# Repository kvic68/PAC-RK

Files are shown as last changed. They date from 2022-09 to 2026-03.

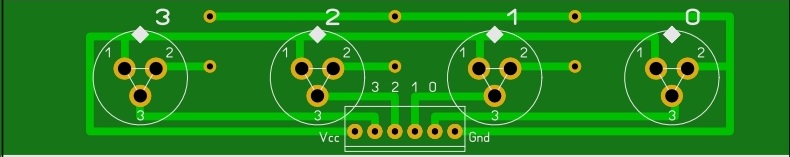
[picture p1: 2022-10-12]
INFO/GX12.JPG

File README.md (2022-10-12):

Предлагаемое устройство представляет собой программно-аппаратный комплекс контроля и управления ректификационной колонной.
Состав комплекса:
- регулятор напряжения со стабилизацией;
- контроллер насоса на шаговом двигателе;
- четырехканальный измеритель температуры с управляющей логикой;
- устройства индикации и управления;
- радио модуль  для удаленного управления по Bluetooth;
- измеритель атмосферного давления на BMP180. Реализует функцию показометра, ничем не   управляет. Можно смотреть динамику атмосферного давления во внешней программе;
- программное обеспечение для удаленного управления, логирования, медитации на разноцветные графики (под Windows).

Обсуждение тут: https://alcodistillers.ru/forum/viewtopic.php?id=2110

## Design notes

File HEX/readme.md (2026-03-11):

1.	regulator.hex – прошивка стабилизатора, заливать в Atmega328;
2.	control.hex – прошивка контроллера температуры, насоса и прочего, только в Atmega328.

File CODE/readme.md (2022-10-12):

Набор исходных текстов на ассемблере. Выполнено в Avr Studio 4.19 
1.	REGULATOR – исходники стабилизатора;
2.	CONTROL – исходники контроллера температуры, насоса и прочего.

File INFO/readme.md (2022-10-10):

1.	specification.pdf (docx) – описание работы комплекса;
2.	bill-of-materials.pdf (xls) – практически полный список деталей;
3.	scheme.spl7 – схема в формате Splan7.0, sheme.gif – она же картинкой;
4.	plate.lay6 – вариант печатной платы в формате Sprint Layout 6, plate-top.gif и plate-bottom.gif – она же в виде картинок, вид сверху и снизу.

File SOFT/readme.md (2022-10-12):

Программа управления комплексом.
Скопировать оба файла в отдельную папку и запустить исполняемый.

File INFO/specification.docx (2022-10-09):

Предлагаемое устройство представляет собой программно-аппаратный комплекс контроля и управления ректификационной колонной.

Состав комплекса:

- регулятор напряжения со стабилизацией;

- контроллер насоса на шаговом двигателе;

- четырехканальный измеритель температуры с управляющей логикой;

- устройства индикации и управления;

- радио модуль для удаленного управления по Bluetooth;

- измеритель атмосферного давления на BMP180. Реализует функцию показометра, ничем не управляет. Можно смотреть динамику атмосферного давления во внешней программе;

- программное обеспечение для удаленного управления, логирования, медитации на разноцветные графики (под Windows).

Регулятор напряжения

Обеспечивает стабильное напряжение на нагрузке не выше входного.

Работает в трех режимах:

- стабилизация,

- разгон,

- выключено.

Имеет возможность подключения дополнительного устройства нагрева при разгоне.

Есть вход аварийного отключения от внешнего датчика.

Аварийное выключение от внешнего источника одновременно останавливает отбор, включает звуковую и световую сигнализацию и блокирует всё удалённое управление.

Контроллер насоса

Управляет насосом на шаговом двигателе, обеспечивает

- равномерную скорость отбора в диапазоне 10-3000 мл/час,

- измерение общего объема отбора,

- режим дозирования (автостоп при достижении заданного объема отбора 10-5000 мл).

Измеритель температуры.

Использует датчики на базе DS18B20.

Четыре независимых канала реализуют следующие функции:

1. Измерение температуры.
2. Контроль достижения и превышения порога.
3. Исполнение установленных действий при достижении(превышении) порога.
4. Один из каналов (любой) дополнительно может осуществлять функцию «контроль разгона», т.е. при достижении температурой установленной величины, переключать режим работы стабилизатора из «разгон» в «поддержание установленного напряжения». Режим «разгон» включается в модуле стабилизатора, требуемое напряжение там же.

Измерение температуры производится одновременно по четырем независимым каналам. Измеренное значение выводится на дисплей. Если датчик неисправен или отсутствует, выводятся черточки.

Контроль превышения порога может быть либо включен, либо выключен.

Если контроль включен, то при превышении порога в любом случае подается сигнал на один из выходов контроллера. Сигнал имеет уровень логического нуля и может быть использован для управления внешними устройствами.

Кроме этого можно включить дополнительные «реакции»:

- включить звуковой сигнал,

- остановить отбор,

- выключить нагрев.

«Реакции» можно комбинировать.

Реакция «выключить нагрев» приравнена к аварийному сигналу выключения регулятора.

Управление

Осуществляется двумя энкодерами типа EC-11 со встроенной кнопкой. Один управляет регулятором напряжения, второй – контроллером насоса и, через систему меню, настройками измерителя температуры, режимами отбора, калибровкой насоса, контролем режима разгона.

Индикация

Всё выводится на OLED дисплей размером 2.42’ или более, разрешением 128х64.

Регулятор напряжения имеет свой OLED дисплей размером 0.96 дюйма. Не обязателен.

Оба дисплея должны иметь подключение по шине i2c.

Основной экран

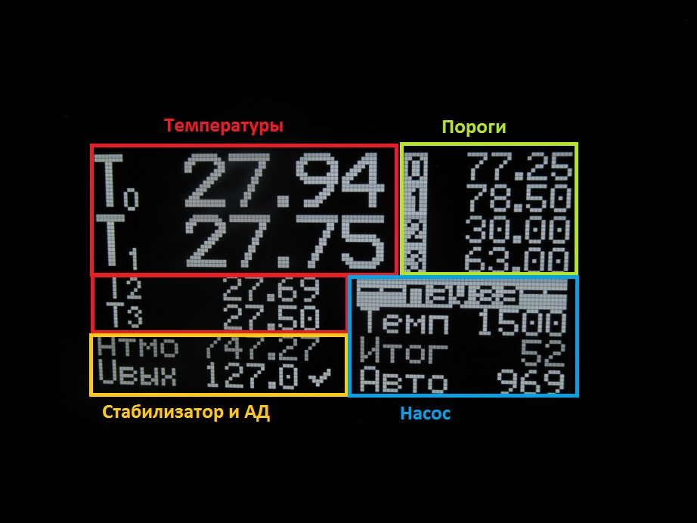
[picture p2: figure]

Блок температур просто отображает значения температуры, измеренные соответствующими датчиками. Если датчик отсутствует или выдаёт некорректные значения, то на дисплей выводится --.--

Блок порогов показывает установленные пороги срабатывания для каждого из датчиков независимо от наличия датчика. Номер датчика отображается в инверсном виде, если установлена какая-нибудь реакция на превышение порога, иначе отображение номера датчика неинверсное. При срабатывании датчика значение порога выводится в инвертированном виде.

Атмосферное давление просто выводится как информация к размышлению.

Насосная часть показывает текущее состояние насоса, скорость отбора мл/час, общий счетчик отбора в мл, остаток до автостопа в мл.

Энкодер №1, управление стабилизатором напряжения.

Логика работы.

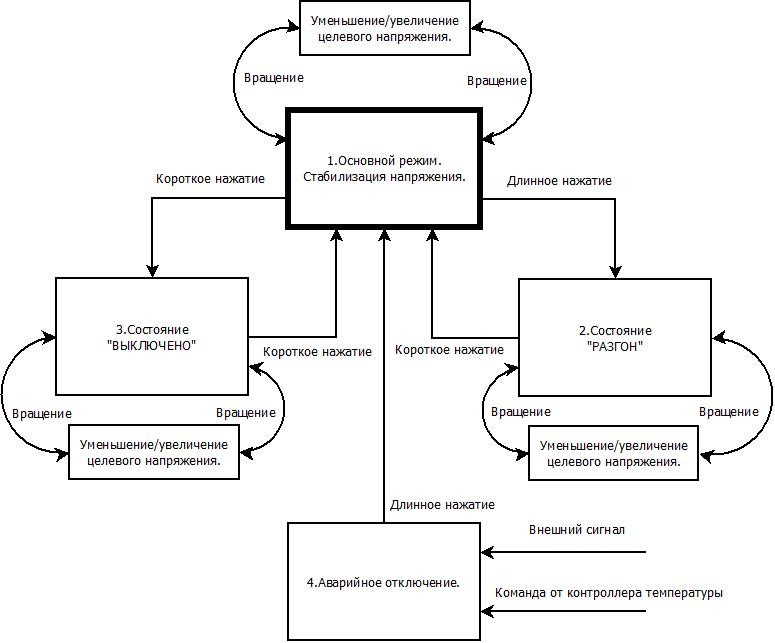
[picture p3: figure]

Отображение режимов работы стабилизатора(примеры).

1.Режим стабилизации.

Справа от значения выходного напряжения значок стабилизации. Показывает, что напряжение находится в коридоре +-0.3 вольта от заданного.

Установка желаемого напряжения призводится вращением ручки энкодера.

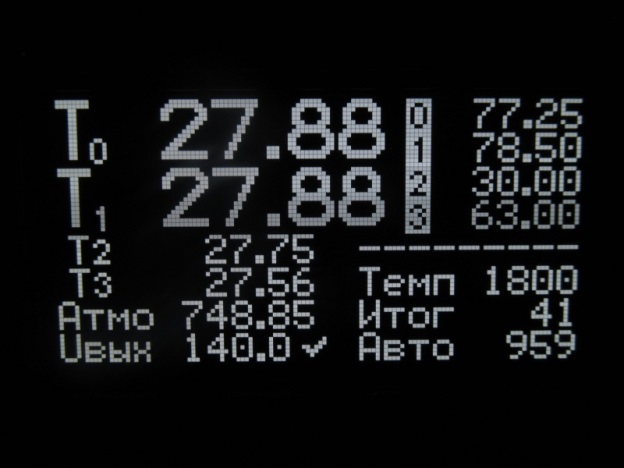
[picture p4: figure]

2.Режим разгона, включен контроль по датчику Т1 при достижении 60 градусов разгон будет выключен и осуществлён переход к напряжению стабилизации 140.0 вольт(в данном случае).

Установка напряжения стабилизации – вращением энкодера.

Вход в режим – длинное нажатие, выход – короткое нажатие.

2.Режим разгона без контроля температуры.

Всё то же самое, только разгон будет продолжаться до бесконечности, если только не отработает реакцию выключения нагрева один из датчиков. Но это уже будет аварийное отключение.

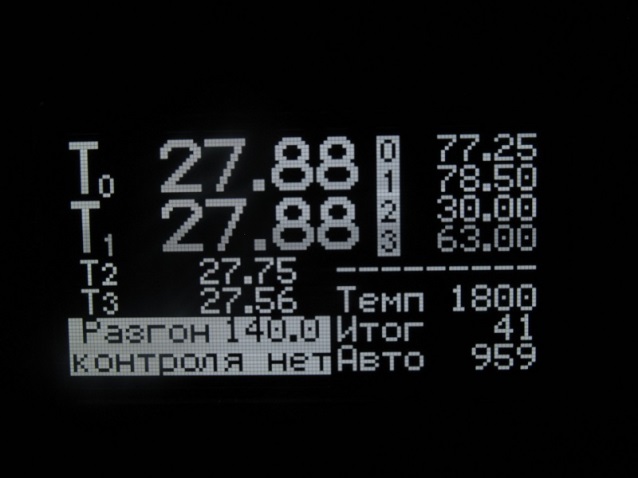
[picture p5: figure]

3.Принудительное отключение нагрева.

Вход в режим и выход из него – короткое нажатие.

4.Отключение аварийным сигналом.

Аварийный сигнал может быть подан на вход устройства либо сгенерирован блоком измерения и контроля температур.

Выход из режима – длинное нажатие на энкодер регулятора напряжения. Если аварийный сигнал не снят, произойдет возврат в режим аварийного отключения.

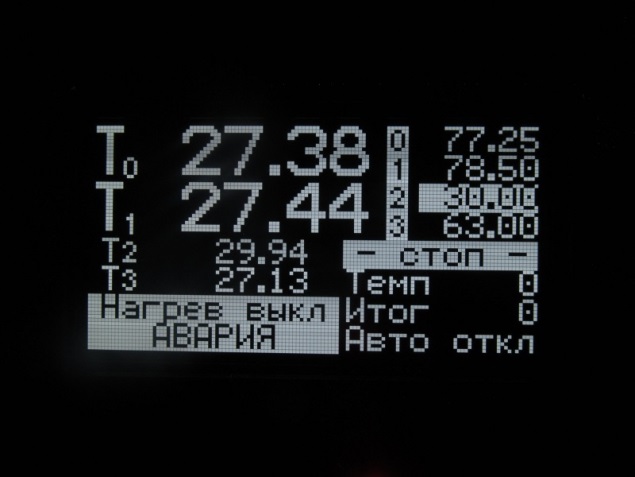
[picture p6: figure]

Энкодер №2, управление насосом и настройками аппарата.

Логика работы.

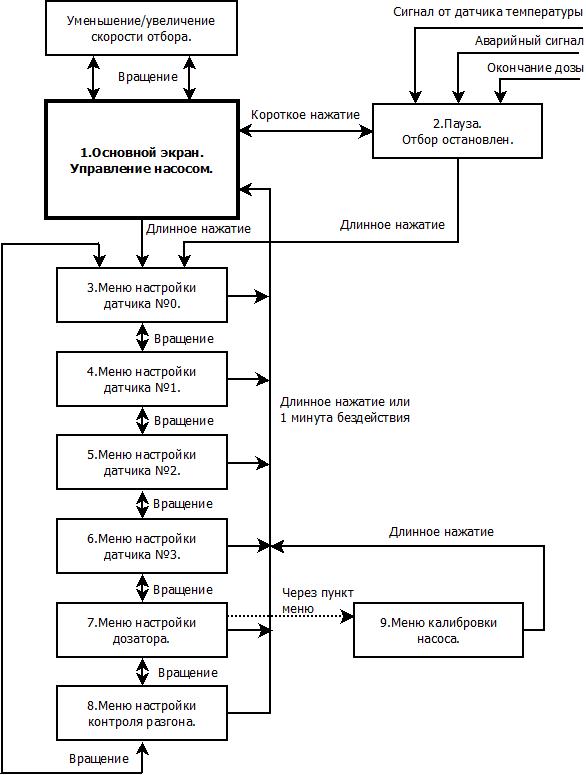
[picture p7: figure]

1.Основной экран.

Вращение энкодера №2 в основном экране приводит к изменению скорости отбора.

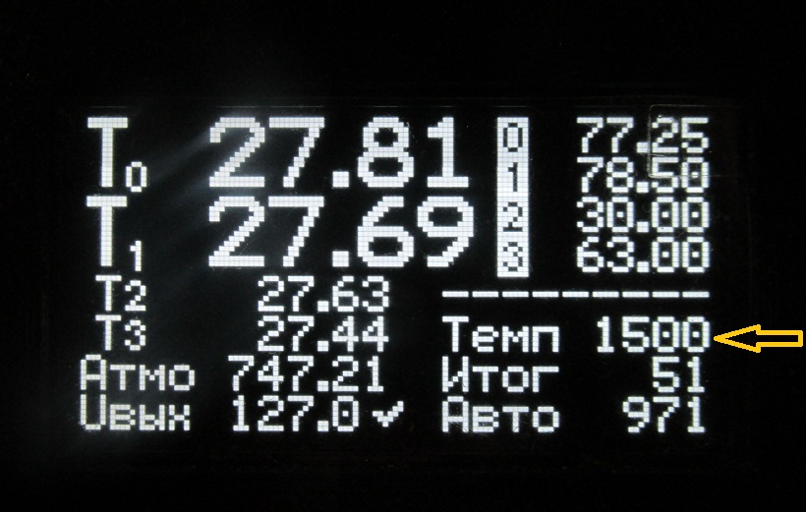
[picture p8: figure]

2. Короткое нажатие (клик) – пауза или продолжение отбора.

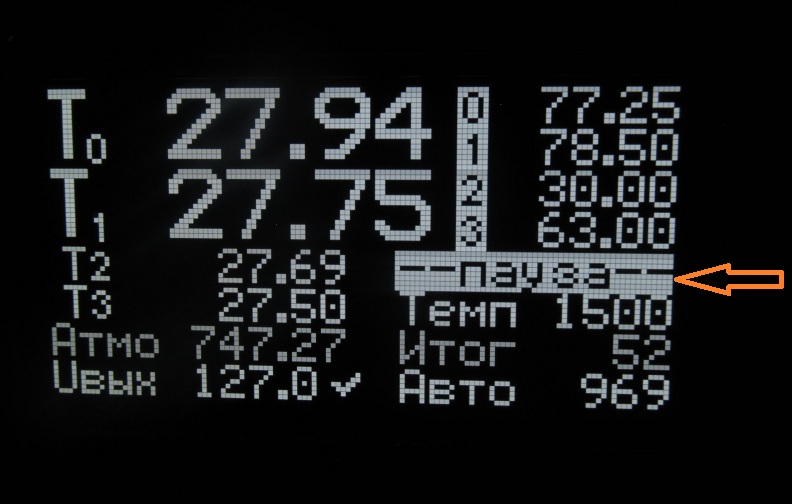
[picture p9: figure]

Длинное нажатие как в режиме рабочего хода, так и в паузе, вызывает переход к выбору экранов настройки температурных датчиков, настройки шага автостопа(дозатор), контроля разгона, калибровки насоса. Выбор датчика или другой настройки осуществляется вращением энкодера. Переход к настройке – короткое нажатие(клик).

3.4.5.6. Меню настройки температурного датчика 0.1.2.3.

Логика настройки температурного датчика.

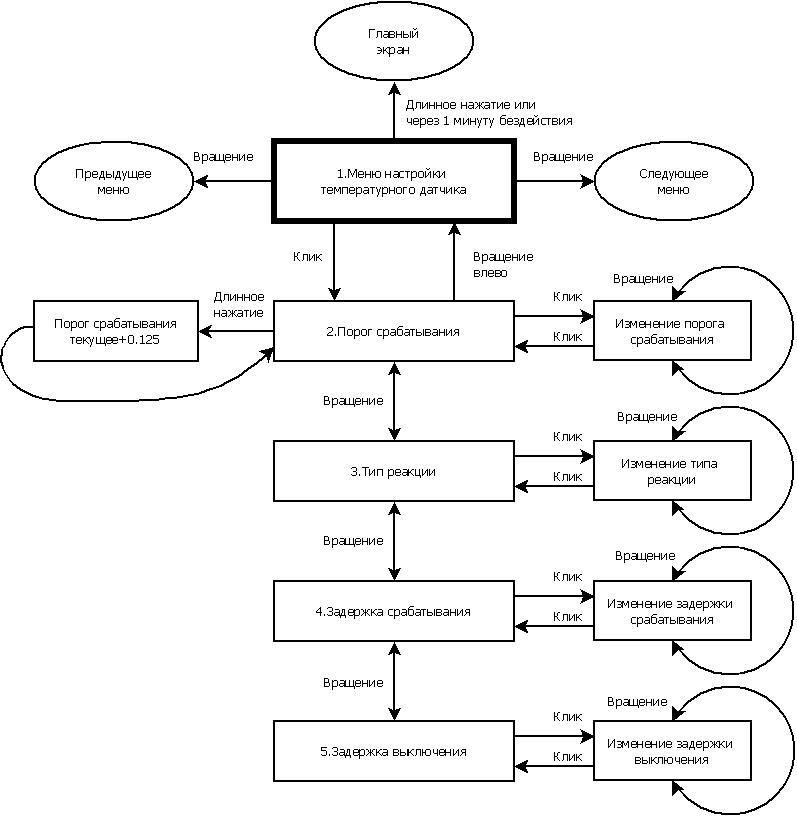
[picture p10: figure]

Порог срабатывания – величина температуры, при которой будут произведены действия, настроенные в пункте «Тип реакции».

Типы реакции:

1. Включить сигнализацию. *
2. Включить звуковой сигнал. ♩
3. Остановить отбор. ││
4. Выключить нагрев. ↓

Последовательность переключения реакций:

- выключено всё;

- включено(выдаёт сигнал на выход и зажигает

индикатор, если он установлен); *

- включено+звук; * ♩

- включено+стоп; * ││

- включено+звук+стоп; * ♩ ││

- включено+нагрев выкл.; * ↓

- включено+звук+нагрев выкл.; * ♩ ↓

- включено+стоп+нагрев выкл.; * ││ ↓

- включено+звук+стоп+нагрев выкл.; * ♩ ││ ↓

«Выключить нагрев» блокирующий. Т.е. при срабатывании этого действия, после остывания датчика автоматический возврат к нагреву не произойдёт. Необходимо участие оператора непосредственно у аппарата. Удалённо включить тоже не получится. Кроме этого при выключении нагрева будет остановлен и блокирован отбор.

Задержка срабатывания – время, которое должно пройти после достижения(превышения) порога до момента срабатывания установленных реакций.

Задержка выключения – то же самое, только при переходе через порог вниз.

Экран настройки датчика (пример):

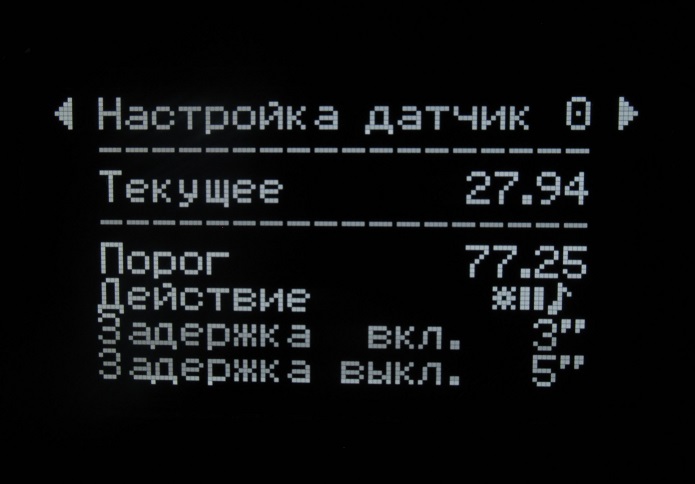
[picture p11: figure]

Температура на датчике 0 равна 27.94 градуса. При достижении значения 77.25 градуса и удержании на этом уровне или выше в течение 3 секунд будет подан сигнал на выход 0, остановлен отбор и включён звуковой сигнал. При снижении температуры ниже порога через 5 секунд будет произведен возврат к нормальному режиму работы.

7. Настройка дозатора.

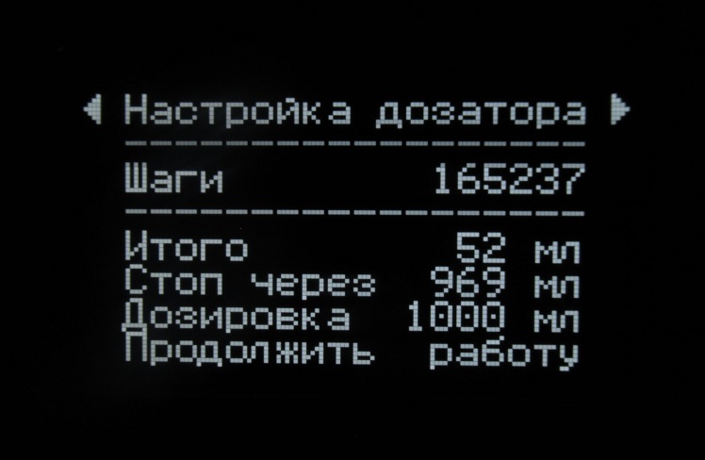
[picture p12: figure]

Доступны три пункта для изменения: «Итого», «Дозировка», «Продолжить…»

Через «Итого» можно сбросить общий счетчик отбора.

«Дозировка» - объем, после которого отбор будет остановлен.

Последний пункт комбинированный, состоит из четырех подпунктов:

- «продолжить работу» – переход в основной экран;

- «продолжить в паузе» – то же самое, только отбор будет на паузе;

- «назад к настройкам» – возврат к настройке дозатора;

- «калибровка насоса» – переход в меню калибровки насоса.

Логика настройки дозатора.

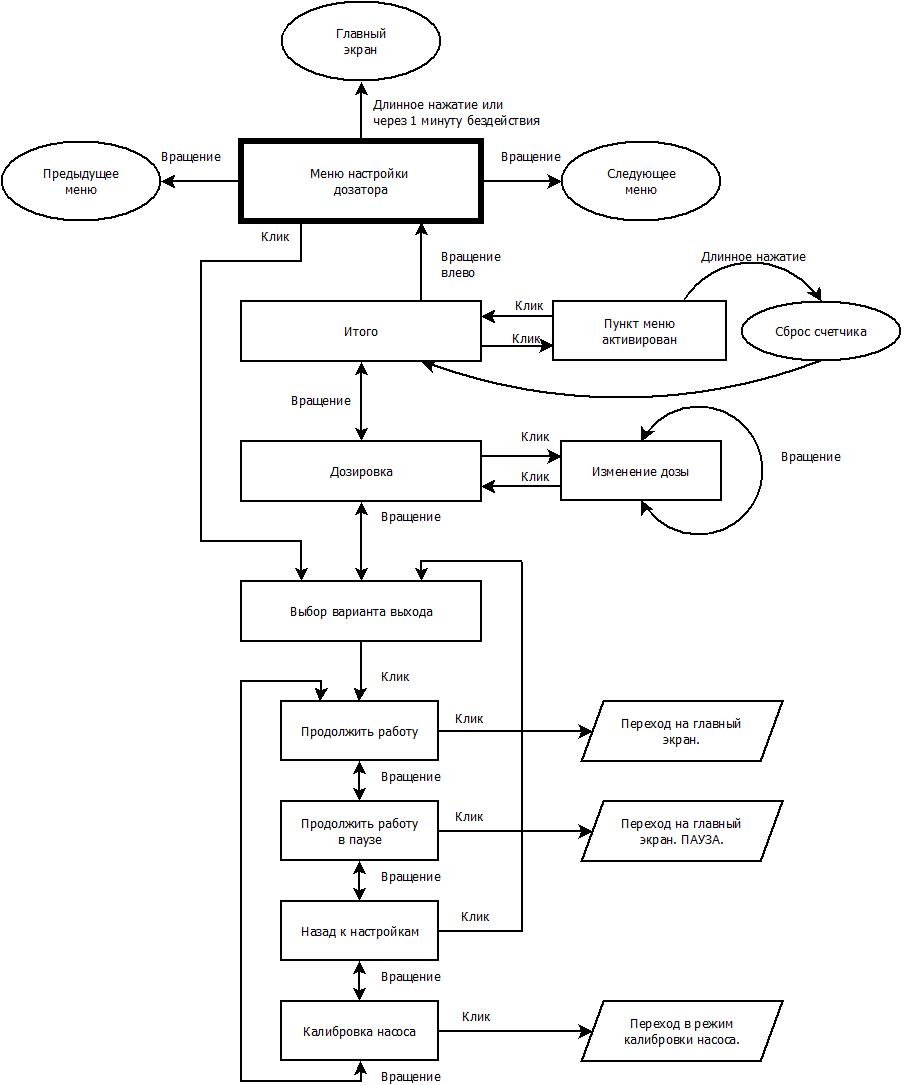
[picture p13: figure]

Режим калибровки насоса.

Доступны строки «Счетчик» и «Записать в «EEPROM».

Логика в режиме калибровки.

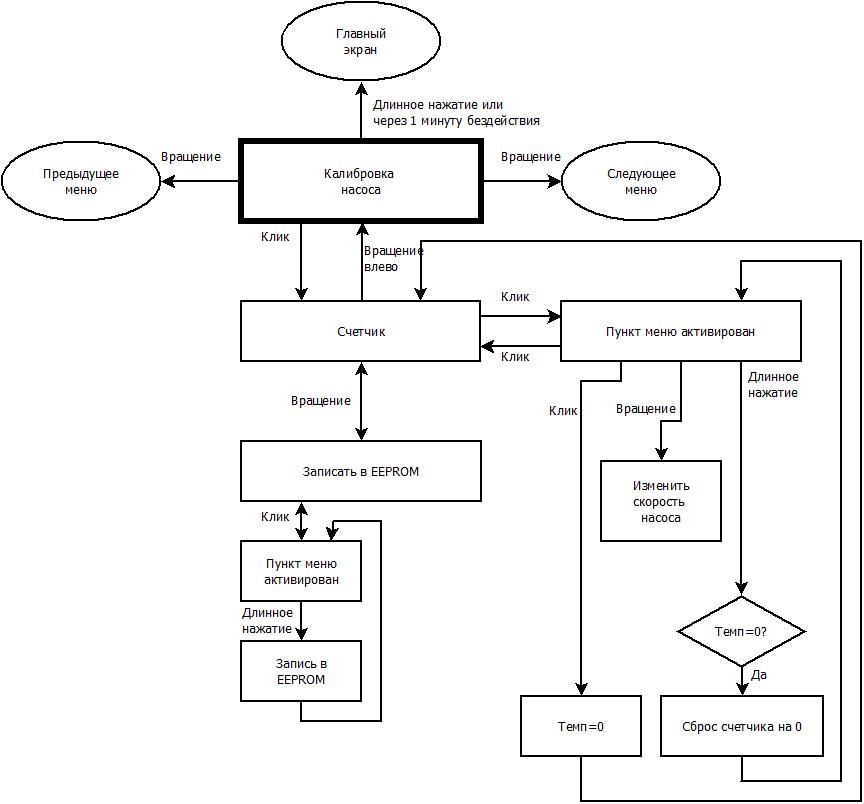
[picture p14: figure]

8. Контроль разгона.

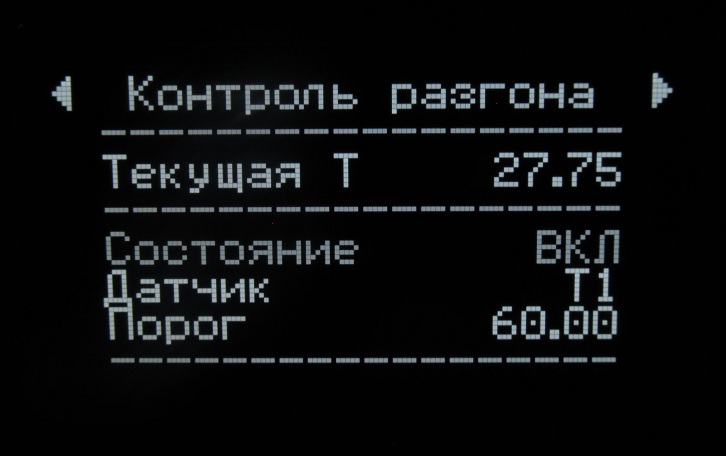
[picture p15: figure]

Можно включить или выключить («Состояние»).

Изменить датчик, осуществляющий контроль («Датчик»).

Изменить порог срабатывания («Порог»).

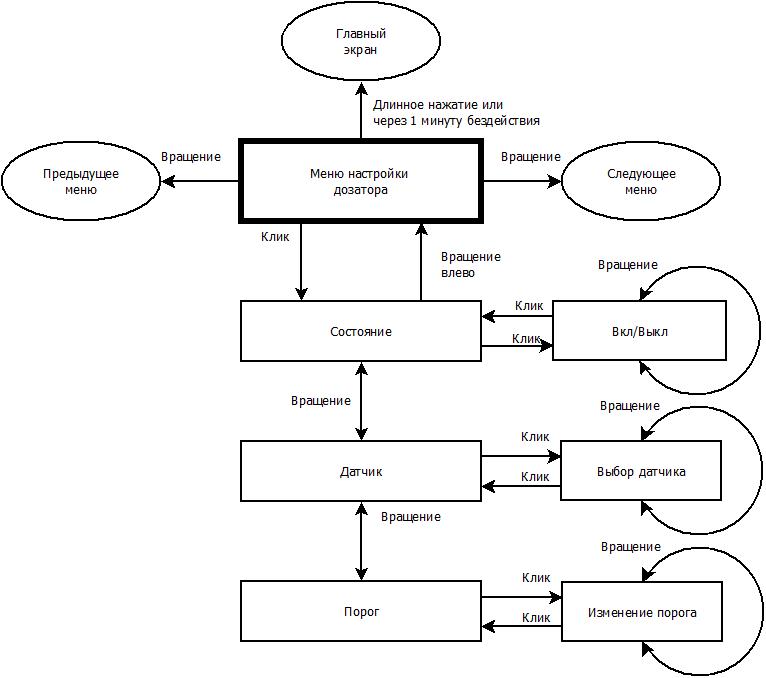
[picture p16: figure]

Программа дистанционного управления «Монитор колонны».

Работает в среде Windows. Достаточно 32-битной версии.

Необходима библиотека sqlite3.dll

Проверено на XP,7,10.

Ресурсов жрёт немного, хватает даже нетбука на Atom-е с 1 Гб памяти.

Связь с основным блоком осуществляется по Bluetooth через COM порт.

При подключении может тупить.

Рисует графики, показывает текущие значения, ведёт лог в текстовом виде(если настроено) и запоминает данные в базе данных SQLite. Просмотровщика базы пока нет.

Даёт возможность удалённо управлять аппаратом.

При наступлении каких-то событий (перегрев по датчику, потеря связи, окончание дозировки) может начать издавать предупреждающие звуки(можно отключить).

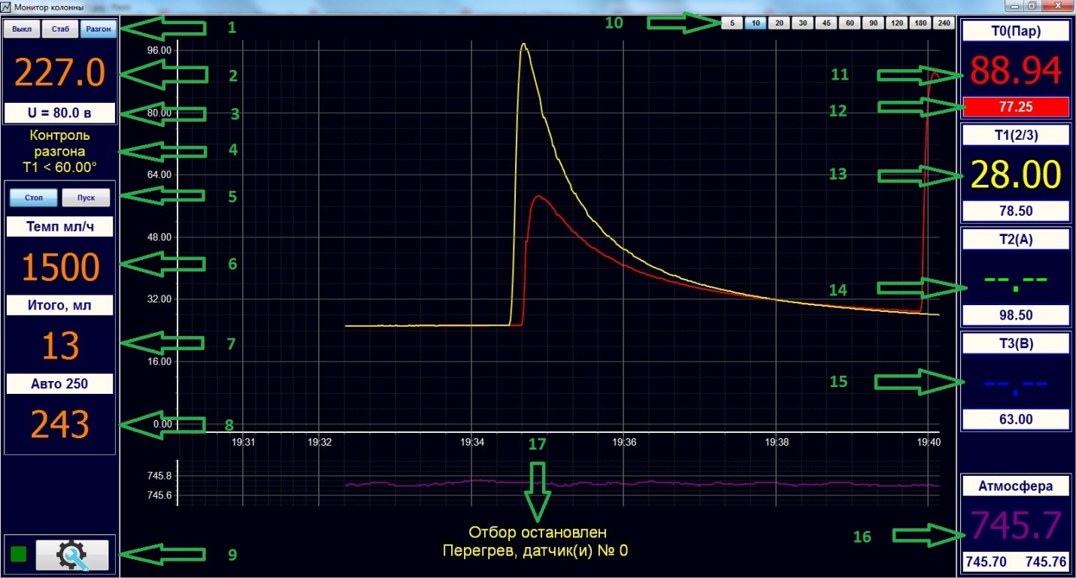
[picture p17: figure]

Все объекты, на которые указывают стрелки, кликабельны и отзываются на кнопки или комбинации кнопок.

1. Кнопки управления режимом стабилизатора. (Q W E)
2. Напряжение стабилизатора (Ctrl+U).

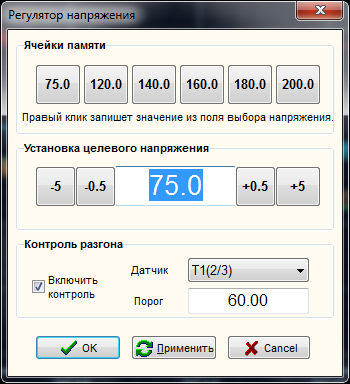
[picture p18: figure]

3. Вычисленная мощность.
4. Состояние контроля разгона. Показывается только при разгоне.
5. Кнопки насоса (Space).
6. Скорость отбора (Ctrl+S).
7. Суммирующий счетчик отбора (Ctrl+X).

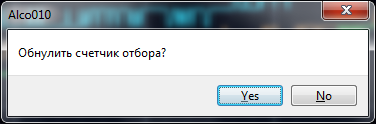
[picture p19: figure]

8. Остаток до автостопа, чуть выше шаг автостопа (Ctrl+A).

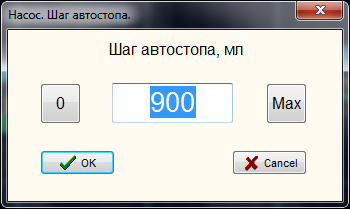
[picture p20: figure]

9. Вызов настроек.

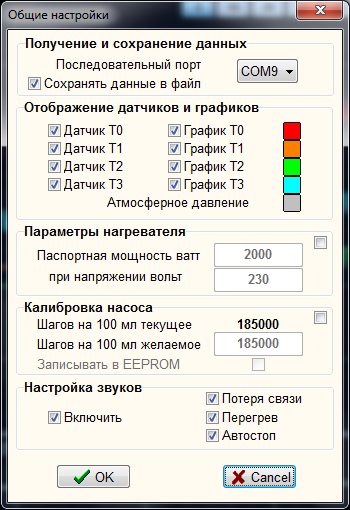
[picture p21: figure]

10. Глубина временнОй шкалы графиков(Alt+0..Alt+9).
11. Датчик Т0 (Ctrl+0)
12. Пороговое значение датчика. В данном случае Т0.
13. Датчик Т1 (Ctrl+1)

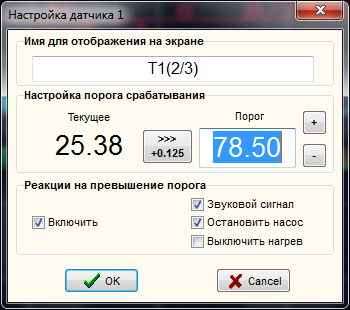
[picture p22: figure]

14. Датчик Т2 (Ctrl+2)

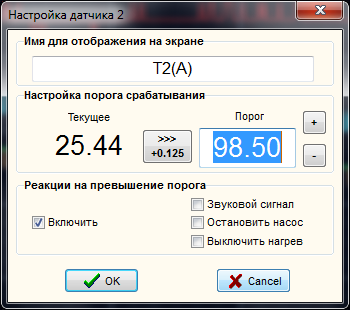
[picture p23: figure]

15. Датчик Т3 (Ctrl+3)

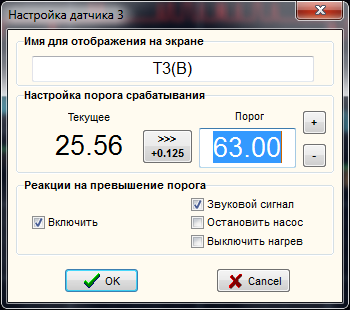
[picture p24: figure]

16. Датчик атмосферного давления.
17. Окно сообщений. Показывается, когда есть что сообщить.

При нажатии на F1 увидим такое:

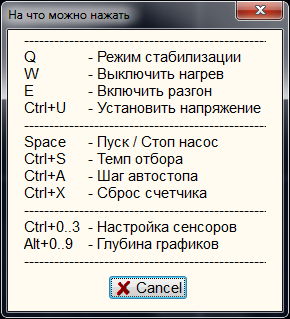
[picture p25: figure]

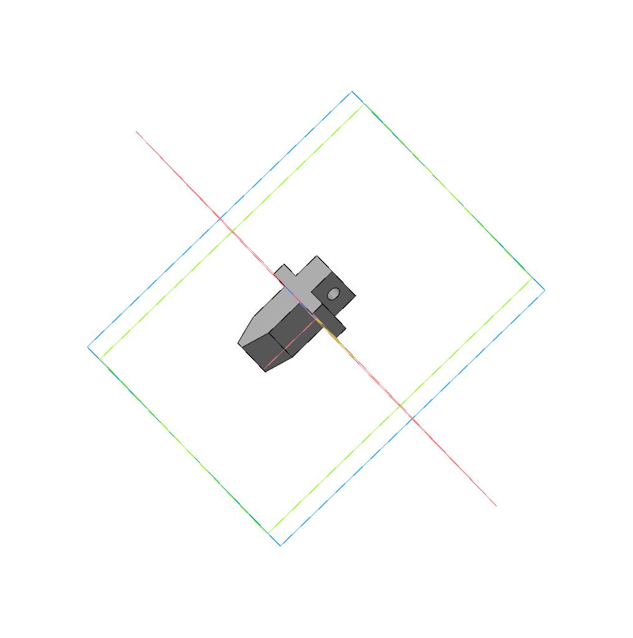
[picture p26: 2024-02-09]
PUMP/LH-625/jpg/клин.jpg

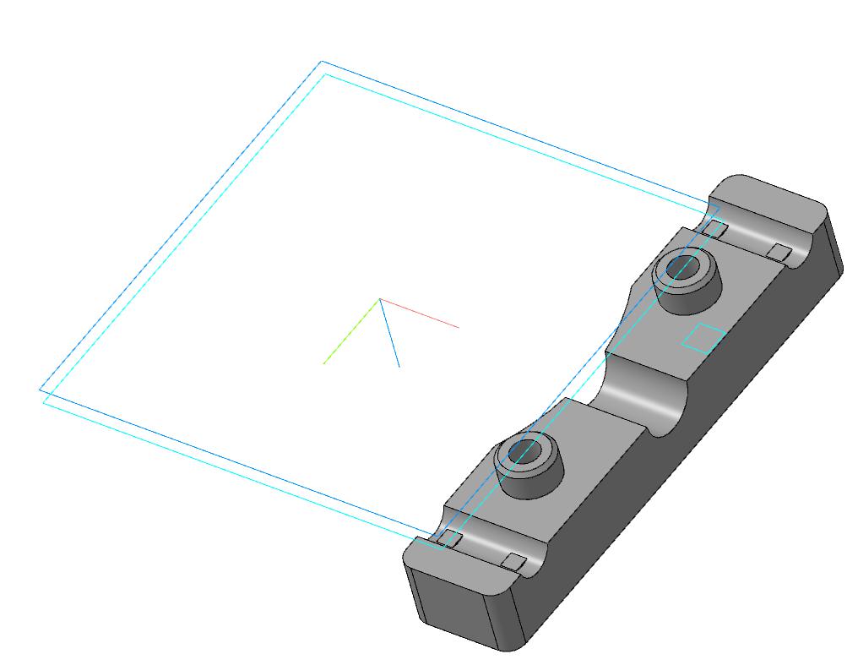
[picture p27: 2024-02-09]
PUMP/LH-625/jpg/статор прижим трубок.jpg

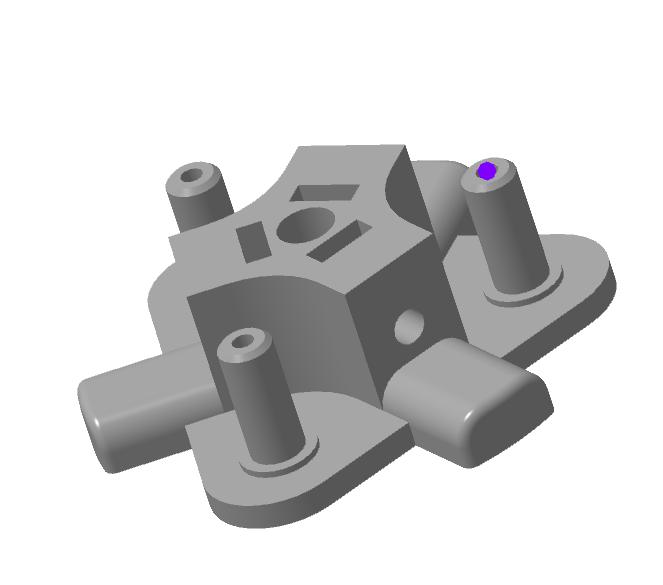
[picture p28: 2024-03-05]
PUMP/LH-625/jpg/ротор основание 625 под саморез.jpg

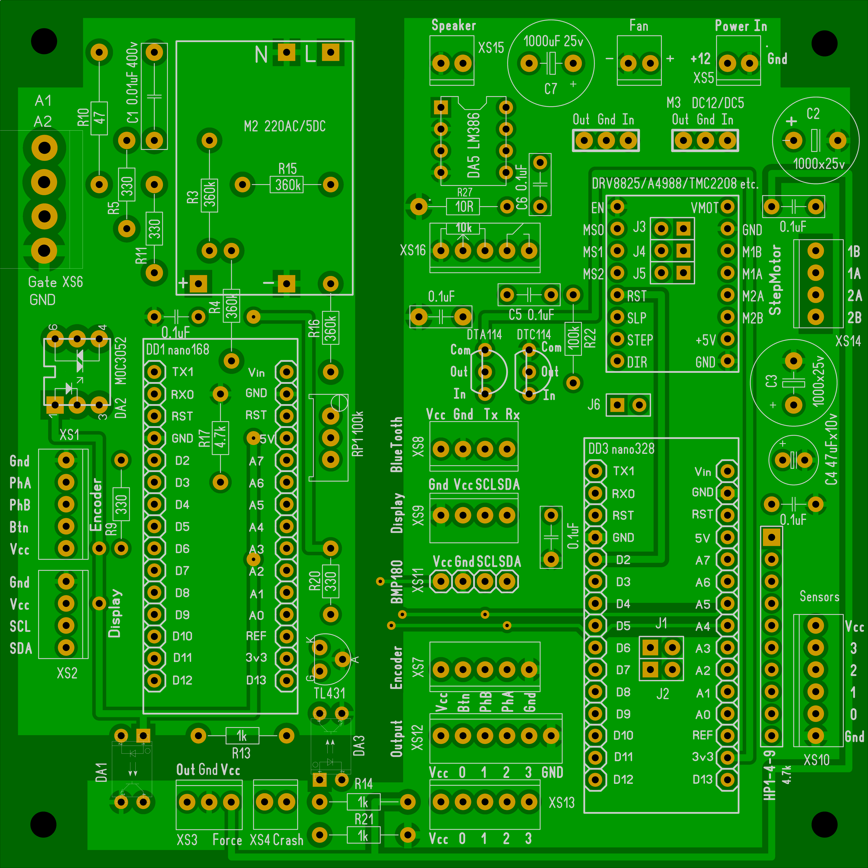
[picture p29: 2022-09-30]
INFO/plate-top.GIF

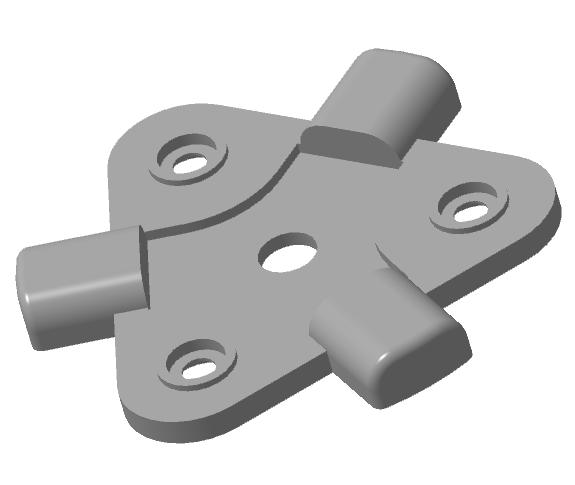
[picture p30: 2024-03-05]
PUMP/LH-625/jpg/ротор крышка 625 под саморез.jpg

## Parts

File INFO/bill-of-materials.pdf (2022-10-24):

Обозначение | Кол-во | Номинал
B1,B2,B3,B4 | 4 | DS18B20
C1 | 1 | 22n 400V | полимерный 10-47nF не менее 400 вольт
C4 | 1 | 47µ 10v | 10-100 микрофарад, не критично
C2,C3,C7 | 3 | 1000µ 25v | можно больше, меньше нежелательно
C5,C6 | 2 | 0,1µ
DA2 | 1 | MOC3052 | годится MOC3023
DA4 | 1 | TL431
DA5 | 1 | LM386
DA6 | 1 | StepMotorDriver | A4988,DRV8825,TMC2208…
DA1,DA3 | 2 | PC817 | любой транзисторный оптрон
DD2 | 1 | ADUM1250
DD1,DD3 | 2 | Arduino nano | можно 168+328
HL1,HL2,HL3,HL4 | 4 | Red Led | любой светодиод, любого цвета, не обязателен
J1,J2,J3,J4,J5,J6 | 6 | jumper | просто перемычка
M 1 | 1 | 0.96 OLED I2C | любой I2C с системой команд SSD1306, не обязателен
M 2 | 1 | 220AC/5DC | AC/DC преобразователь
M 3 | 1 | 12DC/5DC | DC/DC преобразователь
M 4 | 1 | HC-05,JDY-33,etc.
M 5 | 1 | 2.42 OLED I2C | любой I2C с системой команд SSD1306
M 6 | 1 | BMP180
MOT1 | 1 | Step Motor | Nema 17
R10 | 1 | 47 0.5W
R17 | 1 | 4.7k | допуск 1%
R22 | 1 | 100k
R27 | 1 | 10
R1,R2,R6,R7,R8,R 12,R18,R19 | 8 | 4.7k | smd 1206
R13,R14,R21 | 3 | 1k | номинал не критичен, можно до 10 кОм
R23,R24,R25,R26 | 4 | 470 | smd 1206, яркость светодиодов
R3,R4,R15,R16 | 4 | 360k | R15,R16 допуск 1%
R5,R9,R11,R20 | 4 | 330
RP1 | 1 | 100k | многооборотный подстроечник типа 3296
RR1 | 1 | HP1-4-9 4.7k | резисторная сборка можно заменить
RV1 | 1 | 10k | переменный резистор с выключателем
SP | 1 | Speaker | любой маленький динамик от 8 Ом
SW1,SW2 | 2 | Encoder EC11 Type | желательно на круглой плате
VS1 | 1 | BTA41-600
VT1 | 1 | DTA114 | т.н."цифровой транзистор"
VT2 | 1 | DTC114 | т.н."цифровой транзистор"
X1,X2,X3,X4 | 4 | GX12 | Разъёмы подключение датчиков, смотрящие во "внешний мир"
XS3 | 1 | WF3
XS6 | 1 | PWL4
XS1,XS7,XS13,XS1 | 4 | WF5
XS10,XS12 | 2 | WF6
XS2,XS8,XS9,XS11, | 5 | WF4
XS4,XS5,XS15 | 3 | WF2

Ниже разъемы. В принципе любые, какие есть в наличии. Не возбраняется просто запаять.

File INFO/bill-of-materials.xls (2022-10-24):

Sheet: BOM
Обозначение | Кол-во | Номинал
B1,B2,B3,B4 | 4 | DS18B20
C1 | 1 | 22n 400V | полимерный 10-47nF не менее 400 вольт
C4 | 1 | 47µ 10v | 10-100 микрофарад, не критично
C2,C3,C7 | 3 | 1000µ 25v | можно больше, меньше нежелательно
C5,C6 | 2 | 0,1µ
DA2 | 1 | MOC3052 | годится MOC3023
DA4 | 1 | TL431
DA5 | 1 | LM386
DA6 | 1 | StepMotorDriver | A4988,DRV8825,TMC2208…
DA1,DA3 | 2 | PC817 | любой транзисторный оптрон
DD2 | 1 | ADUM1250
DD1,DD3 | 2 | Arduino nano | можно 168+328
HL1,HL2,HL3,HL4 | 4 | Red Led | любой светодиод, любого цвета, не обязателен
J1,J2,J3,J4,J5,J6 | 6 | jumper | просто перемычка
M 1 | 1 | 0.96 OLED I2C | любой I2C с системой команд SSD1306, не обязателен
M 2 | 1 | 220AC/5DC | AC/DC преобразователь
M 3 | 1 | 12DC/5DC | DC/DC преобразователь
M 4 | 1 | HC-05,JDY-33,etc.
M 5 | 1 | 2.42 OLED I2C | любой I2C с системой команд SSD1306
M 6 | 1 | BMP180
MOT1 | 1 | Step Motor | Nema 17
R10 | 1 | 47 0.5W
R17 | 1 | 4.7k | допуск 1%
R22 | 1 | 100k
R27 | 1 | 10
R1,R2,R6,R7,R8,R12,R18,R19 | 8 | 4.7k | smd 1206
R13,R14,R21 | 3 | 1k | номинал не критичен, можно до 10 кОм
R23,R24,R25,R26 | 4 | 470 | smd 1206, яркость светодиодов
R3,R4,R15,R16 | 4 | 360k | R15,R16 допуск 1%
R5,R9,R11,R20 | 4 | 330
RP1 | 1 | 100k | многооборотный подстроечник типа 3296
RR1 | 1 | HP1-4-9 4.7k | резисторная сборка можно заменить отдельными резисторами
RV1 | 1 | 10k | переменный резистор с выключателем
SP | 1 | Speaker | любой маленький динамик от 8 Ом
SW1,SW2 | 2 | Encoder EC11 Type | желательно на круглой плате
VS1 | 1 | BTA41-600
VT1 | 1 | DTA114 | т.н."цифровой транзистор"
VT2 | 1 | DTC114 | т.н."цифровой транзистор"
Ниже разъемы. В принципе любые, какие есть в наличии. Не возбраняется просто запаять.
X1,X2,X3,X4 | 4 | GX12 | Разъёмы подключение датчиков, смотрящие во "внешний мир"
XS3 | 1 | WF3
XS6 | 1 | PWL4
XS1,XS7,XS13,XS16 | 4 | WF5
XS10,XS12 | 2 | WF6
XS2,XS8,XS9,XS11,XS14 | 5 | WF4
XS4,XS5,XS15 | 3 | WF2

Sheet: Картинки
 | Драйвер шагового двигателя
 | Вспомогательный индикатор 0.96 дюйма
 | Преобразователь AC/DC 220/5 вольт
 | Преобразователь DC/DC 12/5 вольт
Bluetooth модуль
 |  |  | Энкодер типа ЕС-11
 |  | Основной индикатор 2.42 дюйма

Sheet: Перемычки
Настройка перемычек для некоторых драйверов.
cостояние перемычек. 0 - разомкнуто, 1 - замкнуто |  |  | величина микрошага
МS1(J3) | МS2(J4) | МS3(J5) | DRV8825 | A4988 | TMC2208
0 | 0 | 0 | 1 | 1 | 0.125
1 | 0 | 0 | 0.5 | 0.5 | 0.5
0 | 1 | 0 | 0.25 | 0.25 | 0.25
1 | 1 | 0 | 0.125 | 0.125 | 0.0625
0 | 0 | 1 | 0.0625
1 | 0 | 1 | 0.03125
0 | 1 | 1 | 0.03125
1 | 1 | 1 | 0.03125 | 0.0625

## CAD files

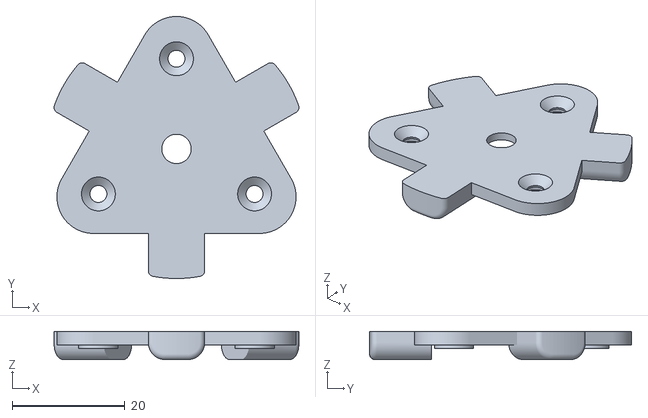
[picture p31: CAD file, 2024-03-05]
PUMP/LH-625/stl/ротор крышка 625 под саморез.stl
43.5 x 46.5 x 5.00

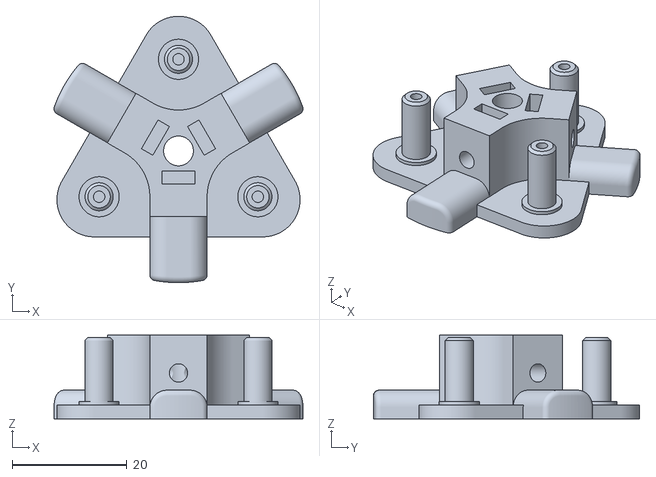
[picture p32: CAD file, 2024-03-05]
PUMP/LH-625/stl/ротор основание 625 под саморез.stl
43.5 x 46.5 x 14.6

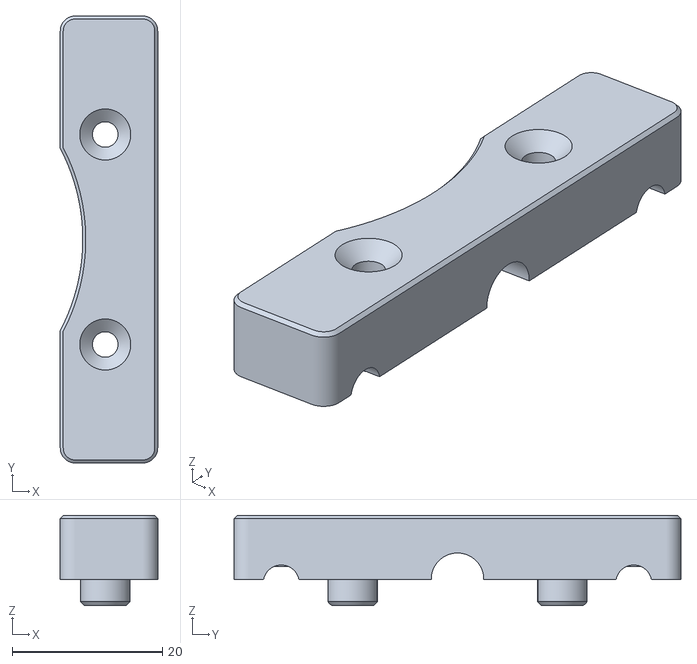
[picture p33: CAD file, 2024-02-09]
PUMP/LH-625/stl/статор прижим трубок.stl
13.0 x 59.6 x 12.0

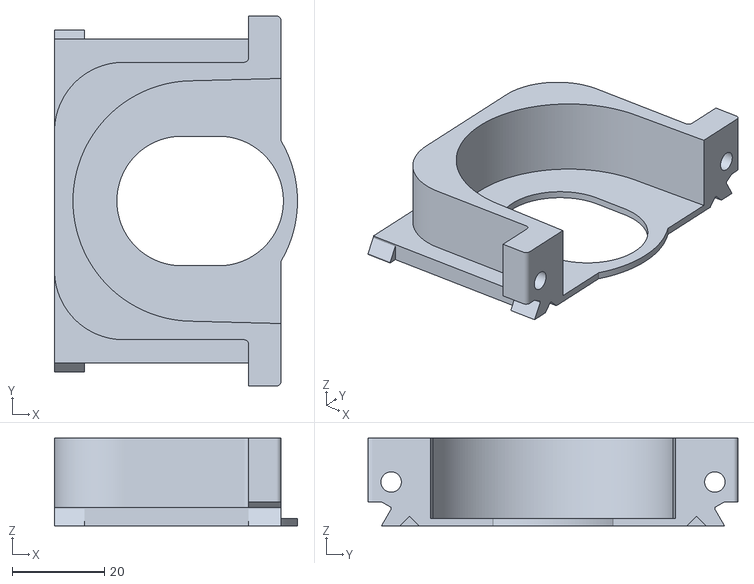
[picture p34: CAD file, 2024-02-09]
PUMP/LH-625/stl/статор подвижная часть ЛХ.stl
52.6 x 80.0 x 19.0

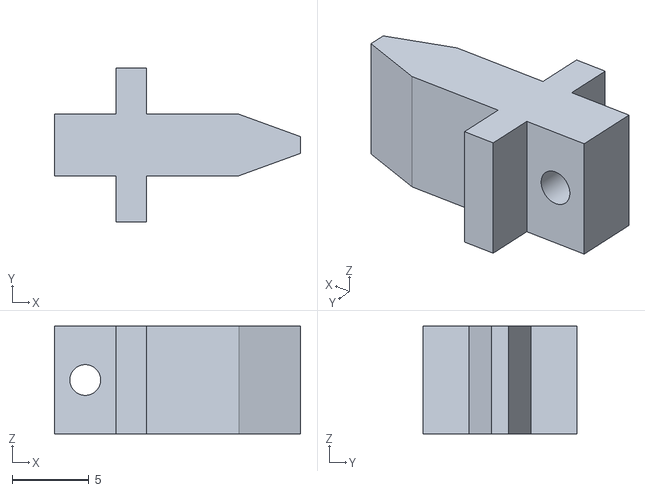
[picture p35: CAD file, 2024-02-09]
PUMP/LH-625/stl/клин.stl
16.0 x 10.0 x 7.00

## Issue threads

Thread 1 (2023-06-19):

Вопрос

GrishaBGA, 2023-06-19:
Вопрос решил повторить ваш контролер, все заработпло кроме енкодера, купил по вашей рекомендации круглые , кнопка нажатия работает а прокрутка нет, и на крнтролере и на регуляторе, может подскажите куда копать, спачибо

kvic68, 2023-06-19:
Приветствую.
На регуляторе уберите резисторы R7,R8.
На контроллере - разомкните J1,J2.
Всё должно заработать.

GrishaBGA, 2023-06-19:
J1, J2 розомкнуты , неработает , дисплей заставил работать 2,42 SSD1309, пришлось правда провод ресет добавить, а енкодер нивкакую :((

--
З повагою Григорій Белик
+380 67 673 30 70

19 червня 2023, 22:52:45, від "kvic68" ***@***.***>:

Приветствую.
На регуляторе уберите резисторы R7,R8.
На контроллере - разомкните J1,J2.
Всё должно заработать.
—
Reply to this email directly, view it on GitHub, or unsubscribe.
You are receiving this because you authored the thread.Message ID: ***@***.***>

--=-rcWEJGfVpgF+03z/HPKZ
Content-Type: text/html; charset="UTF-8"
Content-Transfer-Encoding: base64

PGh0bWw+PGJvZHk+PHNwYW4gc3R5bGU9ImRpc3BsYXk6YmxvY2s7IiBjbGFzcz0ieGZtXzM4OTc4
NTk0Ij48ZGl2PjxzcGFuIHN0eWxlPSJmb250LXNpemU6MTJwdDtsaW5lLWhlaWdodDoxNHB0O2Zv
bnQtZmFtaWx5OkFyaWFsOyIgY2xhc3M9InhmbWMxIj5KMSwgSjIg0YDQvtC30L7QvNC60L3Rg9GC
0YsgLCDQvdC10YDQsNCx0L7RgtCw0LXRgiAsINC00LjRgdC/0LvQtdC5INC30LDRgdGC0LDQstC4
0Lsg0YDQsNCx0L7RgtCw0YLRjCAyLDQyIFNTRDEzMDksINC/0YDQuNGI0LvQvtGB0Ywg0L/RgNCw
0LLQtNCwINC/0YDQvtCy0L7QtCDRgNC10YHQtdGCINC00L7QsdCw0LLQuNGC0YwsINCwINC10L3Q
utC+0LTQtdGAINC90LjQstC60LDQutGD0Y4gOigoPC9zcGFuPjxici8+PC9kaXY+DQo8ZGl2Pjxi
ci8+PC9kaXY+DQo8ZGl2Pg0KPGRpdj48c3BhbiBzdHlsZT0iZm9udC1mYW1pbHk6QXJpYWw7Zm9u
dC1zaXplOjEycHQ7bGluZS1oZWlnaHQ6MTRwdDsiPi0tPC9zcGFuPjwvZGl2Pg0KPGRpdj48c3Bh
biBzdHlsZT0iZm9udC1mYW1pbHk6QXJpYWw7Zm9udC1zaXplOjEycHQ7bGluZS1oZWlnaHQ6MTRw
dDsiPtCXINC/0L7QstCw0LPQvtGOINCT0YDQuNCz0L7RgNGW0Lkg0JHQtdC70LjQujwvc3Bhbj48
L2Rpdj4NCjxkaXY+PHNwYW4gc3R5bGU9ImZvbnQtZmFtaWx5OkFyaWFsO2ZvbnQtc2l6ZToxMnB0
O2xpbmUtaGVpZ2h0OjE0cHQ7Ij4rMzgwIDY3IDY3MyAzMCA3MDwvc3Bhbj48L2Rpdj4NCjwvZGl2
Pg0KPGRpdj48YnIvPjwvZGl2Pg0KPGRpdj48YnIvPjwvZGl2Pg0KPGRpdj48aT48c3BhbiBzdHls
ZT0iZm9udC1zaXplOjEwcHQ7bGluZS1oZWlnaHQ6MTJwdDsiPjxzcGFuIHN0eWxlPSJmb250LWZh
bWlseTpBcmlhbDsiPjE5INGH0LXRgNCy0L3RjyAyMDIzLCAyMjo1Mjo0NSwg0LLRltC0DQogICAg
Imt2aWM2OCIgJmx0Ozwvc3Bhbj48YSBocmVmPSJtYWlsdG86bm90aWZpY2F0aW9uc0BnaXRodWIu
Y29tIiB0YXJnZXQ9Il9ibGFuayI+PHNwYW4gc3R5bGU9ImZvbnQtZmFtaWx5OkFyaWFsOyI+bm90
aWZpY2F0aW9uc0BnaXRodWIuY29tPC9zcGFuPjwvYT48c3BhbiBzdHlsZT0iZm9udC1mYW1pbHk6
QXJpYWw7Ij4mZ3Q7Og0KPC9zcGFuPjwvc3Bhbj48L2k+PC9kaXY+DQo8ZGl2Pjxici8+PC9kaXY+
DQo8YmxvY2txdW90ZSBzdHlsZT0iYm9yZGVyLWxlZnQ6MXB4IHNvbGlkICNjY2NjY2M7bWFyZ2lu
OjBweCAwcHggMHB4IDAuOGV4O3BhZGRpbmctbGVmdDoxZXg7Ij4NCjxkaXYgc3R5bGU9ImRpc3Bs
YXk6YmxvY2s7Ij4NCjxkaXY+PC9kaXY+DQo8ZGl2PtCf0YDQuNCy0LXRgtGB0YLQstGD0Y4uPGJy
Lz4NCtCd0LAg0YDQtdCz0YPQu9GP0YLQvtGA0LUg0YPQsdC10YDQuNGC0LUg0YDQtdC30LjRgdGC
0L7RgNGLIFI3LFI4Ljxici8+DQrQndCwINC60L7QvdGC0YDQvtC70LvQtdGA0LUgLSDRgNCw0LfQ
vtC80LrQvdC40YLQtSBKMSxKMi48YnIvPg0K0JLRgdGRINC00L7Qu9C20L3QviDQt9Cw0YDQsNCx
0L7RgtCw0YLRjC48L2Rpdj4NCjxkaXY+PHNwYW4gc3R5bGU9ImZvbnQtc2l6ZTpzbWFsbDtjb2xv
cjojNjY2OyI+4oCUPGJyLz5SZXBseSB0byB0aGlzIGVtYWlsIGRpcmVjdGx5LCA8YSBocmVmPSJo
dHRwczovL2dpdGh1Yi5jb20va3ZpYzY4L1BBQy1SSy9pc3N1ZXMvMSNpc3N1ZWNvbW1lbnQtMTU5
NzY4Mjc3NCIgdGFyZ2V0PSJfYmxhbmsiIHJlbD0ibm9yZWZlcnJlciBub29wZW5lciI+dmlldyBp
dCBvbiBHaXRIdWI8L2E+LCBvciA8YSBocmVmPSJodHRwczovL2dpdGh1Yi5jb20vbm90aWZpY2F0
aW9ucy91bnN1YnNjcmliZS1hdXRoL0FaWEMzWTVEVklORk80QklLQjdJU0YzWE1DVVlaQU5DTkZT
TTZBQUFBQUFaTUs0SlNBIiB0YXJnZXQ9Il9ibGFuayIgcmVsPSJub3JlZmVycmVyIG5vb3BlbmVy
Ij51bnN1YnNjcmliZTwvYT4uPGJyLz5Zb3UgYXJlIHJlY2VpdmluZyB0aGlzIGJlY2F1c2UgeW91
IGF1dGhvcmVkIHRoZSB0aHJlYWQuPGltZyBzcmM9Imh0dHBzOi8vZ2l0aHViLmNvbS9ub3RpZmlj
YXRpb25zL2JlYWNvbi9BWlhDM1k1SFNZTVBTUUk0TjZLRk1TRFhNQ1VZWkE1Q05GU002QUFBQUFB
Wk1LNEpTQ1dHRzMzTk5WU1c0NUM3T1I0WEFaTk1KRlpYRzVMRklOWFcyM0xGTloyS1VZM1BOVldX
SzNUVUw1VVdKVFM3SEsyRk0uZ2lmIiBoZWlnaHQ9IjEiIHdpZHRoPSIxIiBhbHQ9IiIvPjwvc3Bh
bj48c3BhbiBzdHlsZT0iZm9udC1zaXplOjA7Y29sb3I6dHJhbnNwYXJlbnQ7ZGlzcGxheTpub25l
O292ZXJmbG93OmhpZGRlbjt3aWR0aDowO2hlaWdodDowO21heC13aWR0aDowO21heC1oZWlnaHQ6
MDsiPk1lc3NhZ2UgSUQ6ICZsdDtrdmljNjgvUEFDLVJLL2lzc3Vlcy8xLzE1OTc2ODI3NzRAZ2l0
aHViLmNvbSZndDs8L3NwYW4+PC9kaXY+DQo8L2Rpdj4NCjwvYmxvY2txdW90ZT48L3NwYW4+PC9i
b2R5PjwvaHRtbD4NCg==

--=-rcWEJGfVpgF+03z/HPKZ--

GrishaBGA, 2023-06-19:
Да и еще вопос зачем нейтраль пускать на опщий минус, я побоялса так делать разрезал этот узел, возможно зря??

--
З повагою Григорій Белик
+380 67 673 30 70

19 червня 2023, 22:58:05, від "Белик Григорій" ***@***.***>:

J1, J2 розомкнуты , неработает , дисплей заставил работать 2,42 SSD1309, пришлось правда провод ресет добавить, а енкодер нивкакую :((

--
З повагою Григорій Белик
+380 67 673 30 70

19 червня 2023, 22:52:45, від "kvic68" ***@***.***>:

Приветствую.
На регуляторе уберите резисторы R7,R8.
На контроллере - разомкните J1,J2.
Всё должно заработать.
—
Reply to this email directly, view it on GitHub, or unsubscribe.
You are receiving this because you authored the thread.Message ID: ***@***.***>

--=-Mh3R/5+n1Y2T+7LwaMl/
Content-Type: text/html; charset="UTF-8"
Content-Transfer-Encoding: base64

PGh0bWw+PGJvZHk+PHNwYW4gc3R5bGU9ImRpc3BsYXk6YmxvY2s7IiBjbGFzcz0ieGZtXzQxMDAz
NjkzIj48ZGl2PjxzcGFuIHN0eWxlPSJmb250LXNpemU6MTJwdDtsaW5lLWhlaWdodDoxNHB0O2Zv
bnQtZmFtaWx5OkFyaWFsOyIgY2xhc3M9InhmbWMxIj7QlNCwINC4INC10YnQtSDQstC+0L/QvtGB
INC30LDRh9C10Lwg0L3QtdC50YLRgNCw0LvRjCDQv9GD0YHQutCw0YLRjCDQvdCwINC+0L/RidC4
0Lkg0LzQuNC90YPRgSwg0Y8g0L/QvtCx0L7Rj9C70YHQsCDRgtCw0Log0LTQtdC70LDRgtGMINGA
0LDQt9GA0LXQt9Cw0Lsg0Y3RgtC+0YIg0YPQt9C10LssINCy0L7Qt9C80L7QttC90L4g0LfRgNGP
Pz88L3NwYW4+PGJyLz48L2Rpdj4NCjxkaXY+PGJyLz48L2Rpdj4NCjxkaXY+DQo8ZGl2PjxzcGFu
IHN0eWxlPSJmb250LWZhbWlseTpBcmlhbDtmb250LXNpemU6MTJwdDtsaW5lLWhlaWdodDoxNHB0
OyI+LS08L3NwYW4+PC9kaXY+DQo8ZGl2PjxzcGFuIHN0eWxlPSJmb250LWZhbWlseTpBcmlhbDtm
b250LXNpemU6MTJwdDtsaW5lLWhlaWdodDoxNHB0OyI+0Jcg0L/QvtCy0LDQs9C+0Y4g0JPRgNC4
0LPQvtGA0ZbQuSDQkdC10LvQuNC6PC9zcGFuPjwvZGl2Pg0KPGRpdj48c3BhbiBzdHlsZT0iZm9u
dC1mYW1pbHk6QXJpYWw7Zm9udC1zaXplOjEycHQ7bGluZS1oZWlnaHQ6MTRwdDsiPiszODAgNjcg
NjczIDMwIDcwPC9zcGFuPjwvZGl2Pg0KPC9kaXY+DQo8ZGl2Pjxici8+PC9kaXY+DQo8ZGl2Pjxi
ci8+PC9kaXY+DQo8ZGl2PjxpPjxzcGFuIHN0eWxlPSJmb250LXNpemU6MTBwdDtsaW5lLWhlaWdo
dDoxMnB0OyI+PHNwYW4gc3R5bGU9ImZvbnQtZmFtaWx5OkFyaWFsOyI+MTkg0YfQtdGA0LLQvdGP
IDIwMjMsIDIyOjU4OjA1LCDQstGW0LQNCiAgICAi0JHQtdC70LjQuiDQk9GA0LjQs9C+0YDRltC5
IiAmbHQ7PC9zcGFuPjxhIGhyZWY9Im1haWx0bzpiZ2FAdWtyLm5ldCIgdGFyZ2V0PSJfYmxhbmsi
PjxzcGFuIHN0eWxlPSJmb250LWZhbWlseTpBcmlhbDsiPmJnYUB1a3IubmV0PC9zcGFuPjwvYT48
c3BhbiBzdHlsZT0iZm9udC1mYW1pbHk6QXJpYWw7Ij4mZ3Q7Og0KPC9zcGFuPjwvc3Bhbj48L2k+
PC9kaXY+DQo8ZGl2Pjxici8+PC9kaXY+DQo8YmxvY2txdW90ZSBzdHlsZT0iYm9yZGVyLWxlZnQ6
MXB4IHNvbGlkICNjY2NjY2M7bWFyZ2luOjBweCAwcHggMHB4IDAuOGV4O3BhZGRpbmctbGVmdDox
ZXg7Ij4NCjxkaXYgc3R5bGU9ImRpc3BsYXk6YmxvY2s7Ij4NCjxkaXY+PHNwYW4gc3R5bGU9ImZv
bnQtc2l6ZToxMnB0O2xpbmUtaGVpZ2h0OjE0cHQ7Zm9udC1mYW1pbHk6QXJpYWw7Ij5KMSwgSjIg
0YDQvtC30L7QvNC60L3Rg9GC0YsgLCDQvdC10YDQsNCx0L7RgtCw0LXRgiAsINC00LjRgdC/0LvQ
tdC5INC30LDRgdGC0LDQstC40Lsg0YDQsNCx0L7RgtCw0YLRjCAyLDQyIFNTRDEzMDksINC/0YDQ
uNGI0LvQvtGB0Ywg0L/RgNCw0LLQtNCwINC/0YDQvtCy0L7QtCDRgNC10YHQtdGCINC00L7QsdCw
0LLQuNGC0YwsINCwINC10L3QutC+0LTQtdGAINC90LjQstC60LDQutGD0Y4gOigoPC9zcGFuPjwv
ZGl2Pg0KPGRpdj48YnIvPjwvZGl2Pg0KPGRpdj4NCjxkaXY+PHNwYW4gc3R5bGU9ImZvbnQtZmFt
aWx5OkFyaWFsO2ZvbnQtc2l6ZToxMnB0O2xpbmUtaGVpZ2h0OjE0cHQ7Ij4tLTwvc3Bhbj48L2Rp
dj4NCjxkaXY+PHNwYW4gc3R5bGU9ImZvbnQtZmFtaWx5OkFyaWFsO2ZvbnQtc2l6ZToxMnB0O2xp
bmUtaGVpZ2h0OjE0cHQ7Ij7QlyDQv9C+0LLQsNCz0L7RjiDQk9GA0LjQs9C+0YDRltC5INCR0LXQ
u9C40Lo8L3NwYW4+PC9kaXY+DQo8ZGl2PjxzcGFuIHN0eWxlPSJmb250LWZhbWlseTpBcmlhbDtm
b250LXNpemU6MTJwdDtsaW5lLWhlaWdodDoxNHB0OyI+PGEgaHJlZj0idGVsOiszODA2NzY3MzMw
NzAiIGRhdGEtdWtybmV0LXRlbD0iKzM4MDY3NjczMzA3MCIgcmVsPSJub3JlZmVycmVyIG5vb3Bl
bmVyIj4rMzgwIDY3IDY3MyAzMCA3MDwvYT48L3NwYW4+PC9kaXY+DQo8L2Rpdj4NCjxkaXY+PGJy
Lz48L2Rpdj4NCjxkaXY+PGJyLz48L2Rpdj4NCjxkaXY+PGk+PHNwYW4gc3R5bGU9ImZvbnQtc2l6
ZToxMHB0O2xpbmUtaGVpZ2h0OjEycHQ7Ij48c3BhbiBzdHlsZT0iZm9udC1mYW1pbHk6QXJpYWw7
Ij4xOSDRh9C10YDQstC90Y8gMjAyMywgMjI6NTI6NDUsINCy0ZbQtA0KICAgICJrdmljNjgiICZs
dDs8L3NwYW4+PGEgaHJlZj0ibWFpbHRvOm5vdGlmaWNhdGlvbnNAZ2l0aHViLmNvbSIgdGFyZ2V0
PSJfYmxhbmsiPjxzcGFuIHN0eWxlPSJmb250LWZhbWlseTpBcmlhbDsiPm5vdGlmaWNhdGlvbnNA
Z2l0aHViLmNvbTwvc3Bhbj48L2E+PHNwYW4gc3R5bGU9ImZvbnQtZmFtaWx5OkFyaWFsOyI+Jmd0
OzoNCjwvc3Bhbj48L3NwYW4+PC9pPjwvZGl2Pg0KPGRpdj48YnIvPjwvZGl2Pg0KPGJsb2NrcXVv
dGUgc3R5bGU9ImJvcmRlci1sZWZ0OjFweCBzb2xpZCAjY2NjY2NjO21hcmdpbjowcHggMHB4IDBw
eCAwLjhleDtwYWRkaW5nLWxlZnQ6MWV4OyI+DQo8ZGl2IHN0eWxlPSJkaXNwbGF5OmJsb2NrOyI+
DQo8ZGl2PjwvZGl2Pg0KPGRpdj7Qn9GA0LjQstC10YLRgdGC0LLRg9GOLjxici8+DQrQndCwINGA
0LXQs9GD0LvRj9GC0L7RgNC1INGD0LHQtdGA0LjRgtC1INGA0LXQt9C40YHRgtC+0YDRiyBSNyxS
OC48YnIvPg0K0J3QsCDQutC+0L3RgtGA0L7Qu9C70LXRgNC1IC0g0YDQsNC30L7QvNC60L3QuNGC
0LUgSjEsSjIuPGJyLz4NCtCS0YHRkSDQtNC+0LvQttC90L4g0LfQsNGA0LDQsdC+0YLQsNGC0Ywu
PC9kaXY+DQo8ZGl2PjxzcGFuIHN0eWxlPSJmb250LXNpemU6c21hbGw7Y29sb3I6IzY2NjsiPuKA
lDxici8+UmVwbHkgdG8gdGhpcyBlbWFpbCBkaXJlY3RseSwgPGEgaHJlZj0iaHR0cHM6Ly9naXRo
dWIuY29tL2t2aWM2OC9QQUMtUksvaXNzdWVzLzEjaXNzdWVjb21tZW50LTE1OTc2ODI3NzQiIHRh
cmdldD0iX2JsYW5rIiByZWw9Im5vcmVmZXJyZXIgbm9vcGVuZXIiPnZpZXcgaXQgb24gR2l0SHVi
PC9hPiwgb3IgPGEgaHJlZj0iaHR0cHM6Ly9naXRodWIuY29tL25vdGlmaWNhdGlvbnMvdW5zdWJz
Y3JpYmUtYXV0aC9BWlhDM1k1RFZJTkZPNEJJS0I3SVNGM1hNQ1VZWkFOQ05GU002QUFBQUFBWk1L
NEpTQSIgdGFyZ2V0PSJfYmxhbmsiIHJlbD0ibm9yZWZlcnJlciBub29wZW5lciI+dW5zdWJzY3Jp
YmU8L2E+Ljxici8+WW91IGFyZSByZWNlaXZpbmcgdGhpcyBiZWNhdXNlIHlvdSBhdXRob3JlZCB0
aGUgdGhyZWFkLjxpbWcgc3JjPSJodHRwczovL2dpdGh1Yi5jb20vbm90aWZpY2F0aW9ucy9iZWFj
b24vQVpYQzNZNUhTWU1QU1FJNE42S0ZNU0RYTUNVWVpBNUNORlNNNkFBQUFBQVpNSzRKU0NXR0cz
M05OVlNXNDVDN09SNFhBWk5NSkZaWEc1TEZJTlhXMjNMRk5aMktVWTNQTlZXV0szVFVMNVVXSlRT
N0hLMkZNLmdpZiIgaGVpZ2h0PSIxIiB3aWR0aD0iMSIgYWx0PSIiLz48L3NwYW4+PHNwYW4gc3R5
bGU9ImZvbnQtc2l6ZTowO2NvbG9yOnRyYW5zcGFyZW50O2Rpc3BsYXk6bm9uZTtvdmVyZmxvdzpo
aWRkZW47d2lkdGg6MDtoZWlnaHQ6MDttYXgtd2lkdGg6MDttYXgtaGVpZ2h0OjA7Ij5NZXNzYWdl
IElEOiAmbHQ7a3ZpYzY4L1BBQy1SSy9pc3N1ZXMvMS8xNTk3NjgyNzc0QGdpdGh1Yi5jb20mZ3Q7
PC9zcGFuPjwvZGl2Pg0KPC9kaXY+DQo8L2Jsb2NrcXVvdGU+DQo8L2Rpdj4NCjwvYmxvY2txdW90
ZT48L3NwYW4+PC9ib2R5PjwvaHRtbD4NCg==

--=-Mh3R/5+n1Y2T+7LwaMl/--

kvic68, 2023-06-19:
Если нейтраль отрезать от общего, то перестанет работать детектор нуля и измеритель выходного напряжения.
Не надо бояться, делайте нормальный монтаж и всё будет в порядке.
По энкодерам.
Либо энкодеры бракованые, либо ошибка монтажа.
Тут других вариантов практически нет.
Если их поменять местами тоже не работает?
----

GrishaBGA, 2023-06-19:
тогда наверно бракованые, попробую завтра поменять сам енкодер и попробывать на черной плате c CLK правда

--
З повагою Григорій Белик
+380 67 673 30 70

19 червня 2023, 23:04:08, від "kvic68" ***@***.***>:

Если нейтраль отрезать от общего, то перестанет работать детектор нуля и измеритель выходного напряжения.
Не надо бояться, делайте нормальный монтаж и всё будет в порядке.
По энкодерам.
Либо энкодеры бракованые, либо ошибка монтажа.
Тут других вариантов практически нет.
Если их поменять местами тоже не работает?
—
Reply to this email directly, view it on GitHub, or unsubscribe.
You are receiving this because you authored the thread.Message ID: ***@***.***>

--=-FbeWcwPjvN6KruPaZT2/
Content-Type: text/html; charset="UTF-8"
Content-Transfer-Encoding: base64
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

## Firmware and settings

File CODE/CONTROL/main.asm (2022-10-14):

	.include ("m328Pdef.inc")
	.include ("equ.inc")
	.include ("macro.inc")
// ----------------------------------------------------------------
.dseg
	.include ("ramData.inc")
// ----------------------------------------------------------------
.cseg
reset:
// --  Таблица векторов прерываний --------------------------------
	.include ("intvectors.inc")
start:		
// -- Чистим память и регистры ------------------------------------
//
			ldi		ZL,low(SRAM_START)
			ldi		ZH,high(SRAM_START)
			clr		r16
RamFlushCycle:
	    	st		Z+,r16
			cpi		ZH,high(RAMEND)
			brne	RamFlushCycle
			cpi		ZL,low(RAMEND)
			brne	RamFlushCycle
			clr		ZL
			clr		ZH
ClearReg:	st		Z,ZH
        	inc		ZL
        	cpi		ZL,30
        	brne	ClearReg
        	clr		ZL
// -- Настраиваем стек --------------------------------------------
			ldi R16,low(RAMEND)
    		out SPL,r16
    		ldi R16,high(RAMEND)
    		out SPH,r16
// -- переключаем векторы прерываний в нормальный вид
		in r16,(MCUCR)
		SETB r16,IVCE
		mov r17,r16
		CLRB r16,IVSEL
		out (MCUCR),r17
		out (MCUCR),r16
; ----------------------------------------------------------------------------------------
// -- Настраиваем железо ------------------------------------------
		// Порты ввода/вывода ---------
			ldi r16,$FF
			out DDRB,r16
			ldi r16,0b11011111
			out PORTB,r16

			ldi r16,0b00000000
			out DDRC,r16
			ldi r16,0b00110000
			out PORTC,r16

			ldi r16,0b00011110
			out DDRD,r16
			ldi r16,0b11111111
			out PORTD,r16
		// ----------------------------
		// Отключаем тактирование таймеров
			ldi r16,(1<<TSM) | (1<<PSRASY) | (1<<PSRSYNC)
			out GTCCR,r16
		//-----------------------------
		// Таймер 0 -------------------
		// задаёт временные интервалы
			ldi r16,(1<<WGM01)|(0<<WGM00)			; CTC mode
			out TCCR0A,r16	
			ldi r16,(0<<CS02)|(1<<CS01)|(1<<CS00)	; clk/64
			out TCCR0B,r16
			ldi r16,249								; 1000 Hz
			out OCR0A,r16							; 
			ldi r16,(1<<OCIE0A)						; прерывание по совпадению А разрешаем
			sts TIMSK0,r16
		//-----------------------------
		// Таймер 1 -------------------
		// тактирует драйвер ШД
.equ		T1Stop	= 0b00001000	; CTC,	stopped
.equ		T1Run	= 0b00001010	; CTC,	00001yyy: 000 - no clock, 001 - Fclk, 010 - Fclk/8, 011 - Fclk/64, 
									; 100 - Fclk/256, 101 - Fclk/1024, 110 - ext falling, 111 - ext rising
			; ----------
			ldi r16,0b00000000		; 01000000-Toggle OC1A, 00000000-Normal Port op
			sts TCCR1A,r16
				ldi r16,T1Stop
				sts TCCR1B,r16
			ldi r17,high(6250)		; 50 ms
			ldi r16, low(6250)
			sts OCR1AH,r17
			sts OCR1AL,r16
			ldi r16,(1<<OCIE1A)		; прерывание по совпадению
			sts TIMSK1,r16
		//-----------------------------
		// Таймер 2 -------------------
		// используется для генерации звуков
.equ		SoundOn  = 0b00010010
.equ		SoundOff = 0b00000010
			; CTC, 00000010 - normal port op 0100xx10 - toggle OC2A, 0001xx10 - toggle OC2B
			ldi r16,SoundOff		
			sts TCCR2A,r16
			ldi r16,0b00000011		; clk/32;	00000yyy: 000 - no clock, 001 - Fclk, 010 - Fclk/8, 011 - Fclk/32, 
									; 100 - Fclk/64, 101 - Fclk/128, 110 - Fclk/256, 111 - Fclk/1024
			sts TCCR2B,r16
			ldi r16,124	; 2 kHz
			sts OCR2A,r16
			ldi r16,(0<<OCIE2B)|(1<<OCIE2A)|(0<<TOIE2) 
			sts TIMSK2,r16
		//-----------------------------
		// Последовательный порт ------
			ldi r16, low(bauddivider)
			sts UBRR0L,r16
			ldi r16,high(bauddivider)
			sts UBRR0H,r16
			; Прерывания разрешены, прием-передача разрешен.
			ldi r16,(1<<RXEN0)|(1<<TXEN0)|(1<<RXCIE0)|(1<<TXCIE0)|(0<<UDRIE0)
			sts UCSR0B,r16
			; Формат кадра - 8 бит, один стоп бит, четность не проверяется
			ldi r16,(1<<UCSZ01)|(1<<UCSZ00)
			sts UCSR0C,r16
		//-----------------------------
		// I2C интерфейс - 100 кГц (72), 400 кГц (12)
			ldi r16,12
			sts TWBR,r16
			call i2c_stop
		//-----------------------------
		//	call init23017
		; -- настраиваем экран --------
			call initlcd
		; -- очищаем экран ------------
			call clearlcd
		; -- включаем экран ------------
			call LED_ON
				LDZ HELLOSTRING
				call printstring
		//-----------------------------
		// определяем наличие температурных датчиков
initDS18:	call GetPresence
			; -- принудительно ставим 12-бит
			ldi r16,SkipROM
			call WriteByte

			ldi r16,WriteScratchPad
			call WriteByte

			ldi r16,$00
			call WriteByte

			ldi r16,$00
			call WriteByte

			ldi r16,0b01111111
			call WriteByte
			; -- и записываем в EEPROM DS
;				call GetPresence
;				ldi r16,SkipROM
;				call WriteByte
;				ldi r16,CopyScratchPad
;				call WriteByte
;				M_DELAY_US 15000		; задержка 15 мс
;				ldi r16,RecallE2
;				call WriteByte
			; -- запускаем на измерение
			call ds18NewConvert
		//-----------------------------
		// посмотрим наличие BMP180 и, если есть, считаем коэффициенты
			; ---------------------------
			; --- Настройка BMP 180 -----
			call BMPCheck
			lds r16,(BMPPresence)
			tst r16
			brne loadEEValues
			call BMP180_READ_K
			; ---------------------------
			call BMP180_READ_D
			call BMP180_DECODE_NEW
			; --- первоначальное заполнение буфера ---
			ldi r16,BUFLEN	;16
initavgbuf:	call calcAvgPressure
			dec r16
			brne initavgbuf	
		//-----------------------------
		// загружаем настройки из EEPROM
		// или загружаем значения по умолчанию
		//-----------------------------
loadEEValues:	call chekForEEValues

			call initValues

			LDZ BACK_TIMER_T0
			ldi r16,5
			st Z+,r16
			st Z+,r16
			st Z+,r16
			st Z+,r16

		//-----------------------------
		// Включаем тактирование таймеров
			ldi r16,(0<<TSM) | (0<<PSRASY) | (0<<PSRSYNC)
			out GTCCR,r16
			sei
		//-----------------------------
		// выжидаем окончания первого цикла измерений (1 сек)
initwait:	lds r16,(TIMEFLAGS)
			sbrs r16,3
			rjmp initwait
			CLRB r16,3
			sts (TIMEFLAGS),r16
			call ds18ReadData
			call ds18NewConvert
		//-----------------------------
		// выводим экран основного режима
			call clearlcd
				LDZ MAINSCREEN
				call printstring
		//-----------------------------
				ldi r16,T1Run
				sts TCCR1B,r16
				sts (T1Prescaler),r16

lds r16,(A_FLAGS)
SETB r16,0
sts (A_FLAGS),r16
		
	rjmp main
// ----------------------------------------------------------------
// ----------------------------------------------------------------
main:		lds r16,(TIMEFLAGS)
			// ----------
main_T1000:	sbrs r16,3
			rjmp main_T100
				CLRB r16,3
				sts (TIMEFLAGS),r16
				push r16
					call eachSecondSub	; действия, производящиеся каждые 1000 мс
				pop  r16
			// ----------
main_T100:	sbrs r16,2
			rjmp main_T10
				CLRB r16,2
				sts (TIMEFLAGS),r16
				push r16
					call eachTenthSub	; действия, производящиеся каждые 100 мс
				pop  r16
			// ----------
main_T10:	sbrs r16,1
			rjmp main_KR
				CLRB r16,1
				sts (TIMEFLAGS),r16
				push r16
					call eachHundreedthSub	; действия, производящиеся каждые 10 мс
				pop  r16
			// ------------------------------
main_KR:	lds r16,(KEY_FLAGS)
			// ----------
			sbrs r16,rotateR
			rjmp main_KL
				push r16
					call rotateEnc
				pop  r16
				CLRB r16,rotateR
				sts (KEY_FLAGS),r16
			// ----------
main_KL:	sbrs r16,rotateL
			rjmp main_KB
				push r16
					call rotateEnc
					call resetBackCounter0
				pop  r16
				CLRB r16,rotateL
				sts (KEY_FLAGS),r16
			// ----------
main_KB:	sbrs r16,clickBtn
			rjmp main_KH
				push r16
					call KEY_RESET_STATUS_FOR_ALL_BUTTONS
					call shortKeyPress
					call resetBackCounter0
				pop  r16
				CLRB r16,clickBtn
				sts (KEY_FLAGS),r16
			// ----------
main_KH:	sbrs r16,longHold
			rjmp main_A3
				push r16
					call KEY_RESET_STATUS_FOR_ALL_BUTTONS
					call longKeyHold
					call resetBackCounter0
				pop  r16
				CLRB r16,longHold
				sts (KEY_FLAGS),r16
			// ---------- прием по uart
main_A3:	lds r16,(A_FLAGS)
			sbrs r16,3
			rjmp main_A7
				call RX_DECODE
main_A7:	lds r16,(TX_BUSY)
			tst r16
			breq main_A7A
			rjmp main_end
main_A7A:		call TXmanager
main_end:	rjmp main
// ----------------------------------------------------------------
resetBackCounter0:	push r16
					ldi r16,0
					sts (BACKCOUNTER0),r16
					pop r16
					ret
// ----------------------------------------------------------------
defaultValues:	// Значения по умолчанию. Грузятся, если в EEPROM не установлены.
marginsD:		.dw (7725)*16/100, (7850)*16/100, (9850)*16/100, (6300)*16/100
delaysupD:		.db 3,3,3,3
delaysdnD:		.db 5,5,5,5
actionsD:		.db 8+2+1,8+2+1,8,8+1
heatControlD:	.db 1,$FF,$C0,$03
stepsFor100mlD:	.db byte1(defaultStepsFor100ml), byte2(defaultStepsFor100ml), byte3(defaultStepsFor100ml), byte4(defaultStepsFor100ml)
// ----------------------------------------------------------------
.include ("actions.inc")
.include ("bmp180subs.inc")
.include ("fonts.inc")
.include ("eachtimesubs.inc")
.include ("eepromsubs.inc")
.include ("encoder.inc")
.include ("i2c.inc")
.include ("intsubs.inc")
.include ("lcdcontrolsubs.inc")
.include ("math.inc")
.include ("onewiresubs.inc")
.include ("printsubs.inc")
.include ("reactions.inc")
.include ("screens.inc")
.include ("serial.inc")
// ----------------------------------------------------------------
.eseg
.org 100
emargins:				.dw 0,0,0,0
edelaysup:				.db 0,0,0,0
edelaysdn:				.db 0,0,0,0
eactions:				.db 0,0,0,0
EEnStepsFor100ml:		.db 0,0,0,0
HeatSensor:			.db 1
HeatStatus:			.db $FF
HeatMargin:			.dw $03C0	;	порог 60 С

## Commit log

2022-10-24 err corr
    [bill-of-materials.xls]
2022-11-20 add saving margins
    [CONTROL.obj]
2022-12-07 Update monitor.exe
    ESC added
2022-12-09 ротор под 625 на саморезах
2022-12-09 ротор 687 под саморез
2022-12-12 статор
    [stator cover.stl, статор крышка.stl]
2022-12-28 клин
    [клин.stl]
2023-12-01 Create Сборка ЛХ.jpg
2024-02-04 Регулятор. Универсальный.
2024-03-05 rotor modified
    [ротор крышка 625 под саморез.stl, ротор основание 625 под саморез.stl]
2024-05-21 Create pump_for_4х2.4.zip
    3d models for peristaltic pump with pipe size 4x2.4 mm
2025-05-20 Насос для трубки 6х9
2025-05-20 Компас 22
